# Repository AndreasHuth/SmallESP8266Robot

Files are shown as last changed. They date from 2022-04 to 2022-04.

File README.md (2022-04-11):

# Small ESP8266 Robot
## Short Description
This is a small 2-wheel robot project. Normally not very special. 😉

But there some special topics (at least for me 😊)
- My first project with a self developed PCB (made in China)
- Usage of standard components (easy to get and therefore cheap)
- Design with a standard 18650 Lipo (charging with a USB-C connector)
- 3d printed chassis with a nice design (made by me)
- Usage of an ESP8266 (Wemos D1 mini) with some special features:
        - programming via micro usb interface
        - Wifi access point to control the robot (very nice easy web-interface)
                Please have a look @ this repository 😊

## How to use
Please download the whole project and open it direktly in Visual Studio Code. 
PlatformIO Extension is necessary.

## further informations
Needed packages:
	links2004/WebSockets @ ^2.3.5
	bblanchon/ArduinoJson @ 5.13.3
	pololu/VL53L0X @ ^1.3.0

## Links

https://github.com/miharix/miharix-wifi-rc

## further informations / pictures

final robot :-) 

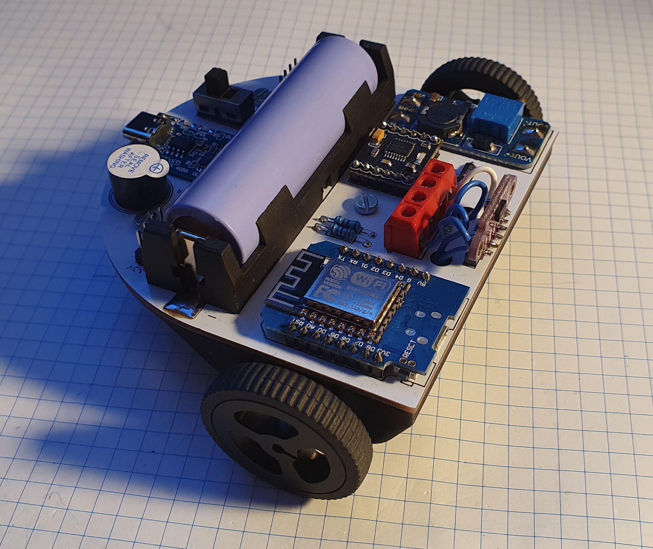
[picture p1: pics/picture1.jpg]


3D model: 

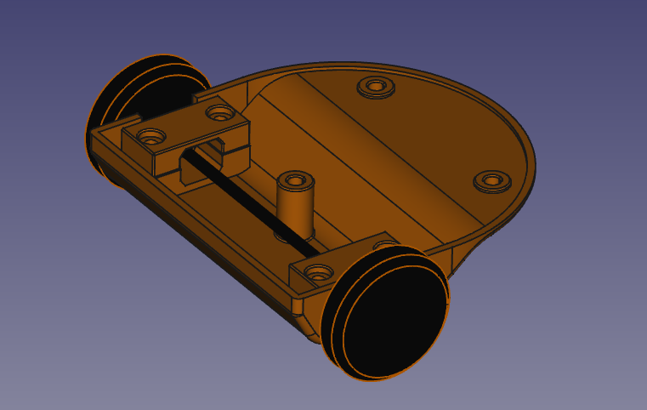
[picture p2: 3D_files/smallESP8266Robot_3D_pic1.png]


link to the schematic:

https://github.com/AndreasHuth/SmallESP8266Robot/blob/master/schematic/Schematic_SmallESP8266Robot.pdf

and partlist:

https://github.com/AndreasHuth/SmallESP8266Robot/blob/master/partlist/part_overview.txt

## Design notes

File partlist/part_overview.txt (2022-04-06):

partlist:
- WEMOS D1 MINI
- VL53LXX
- MOTOR DRIVER
- USB-C 18650 CHARGER
- MT3608 
- Buzzer
- Main switch 
- resistors

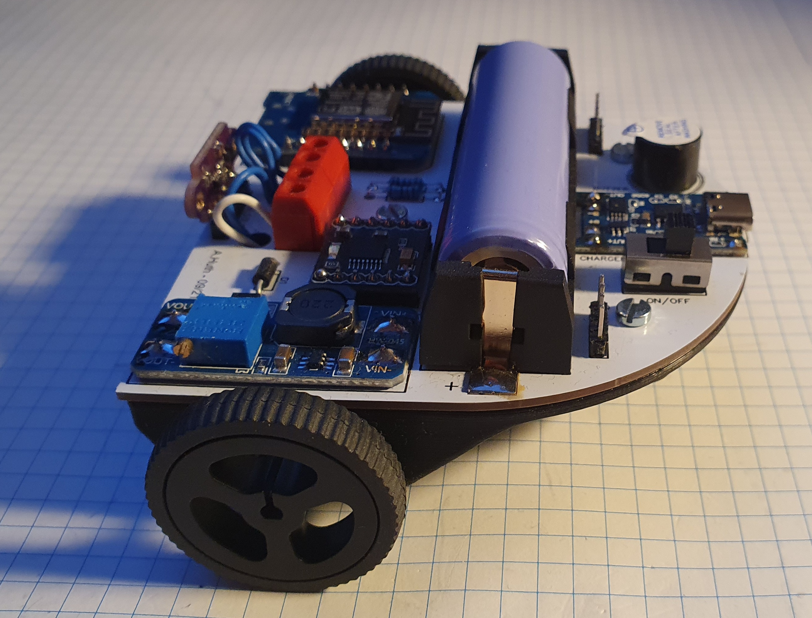
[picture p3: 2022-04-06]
pics/picture3.jpg

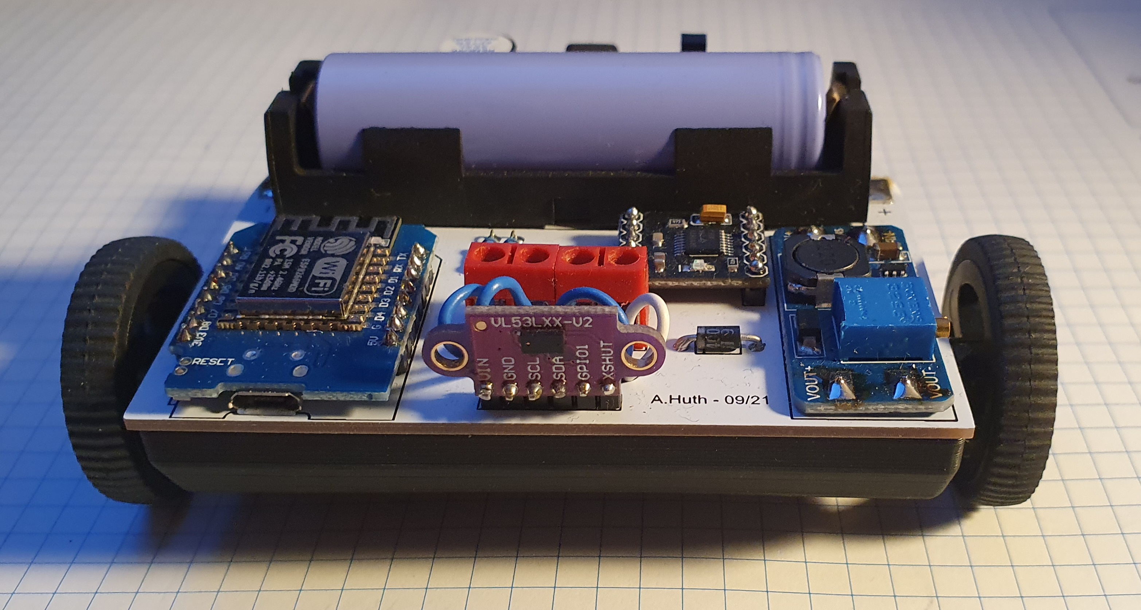
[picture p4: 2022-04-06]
pics/picture4.jpg

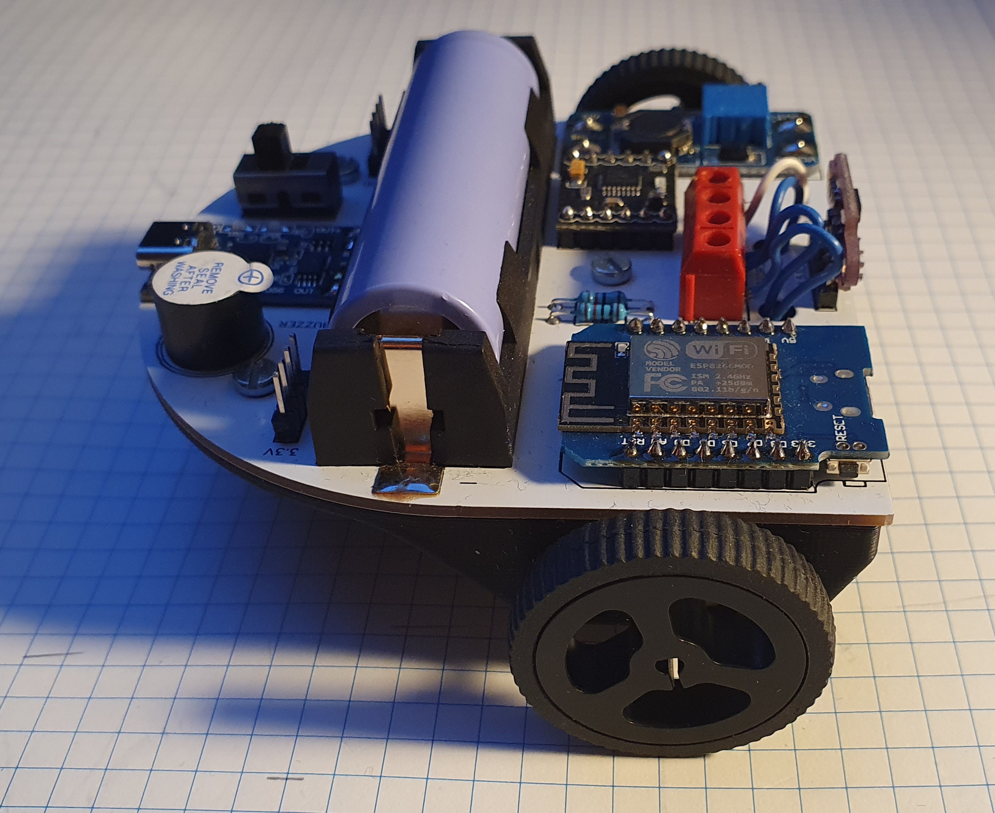
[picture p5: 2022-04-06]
pics/picture5.jpg

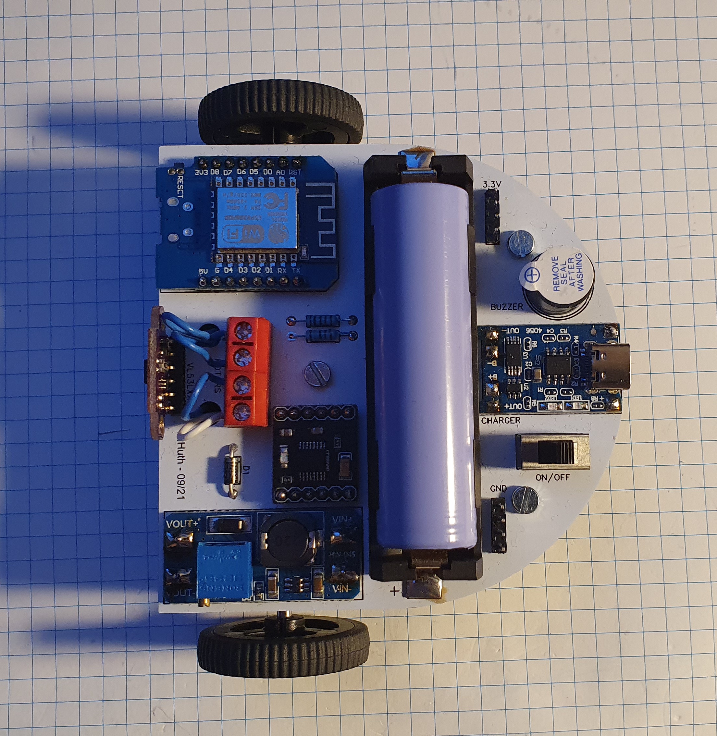
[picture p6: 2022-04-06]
pics/picture2.jpg

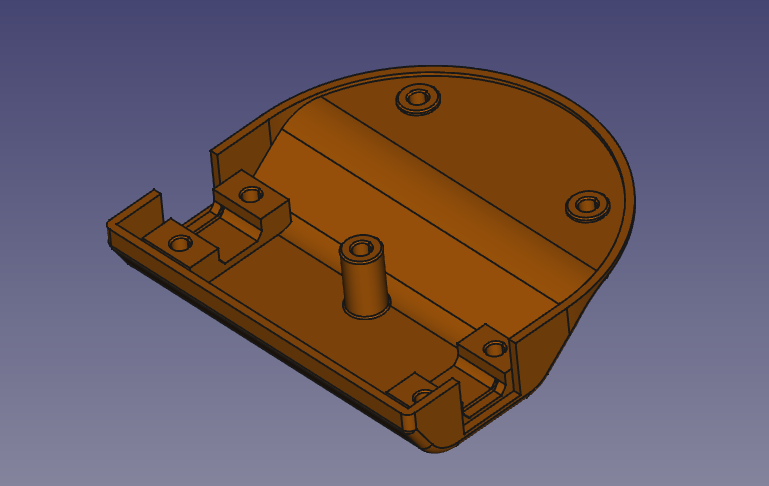
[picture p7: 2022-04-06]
3D_files/smallESP8266Robot_3D_pic2.png

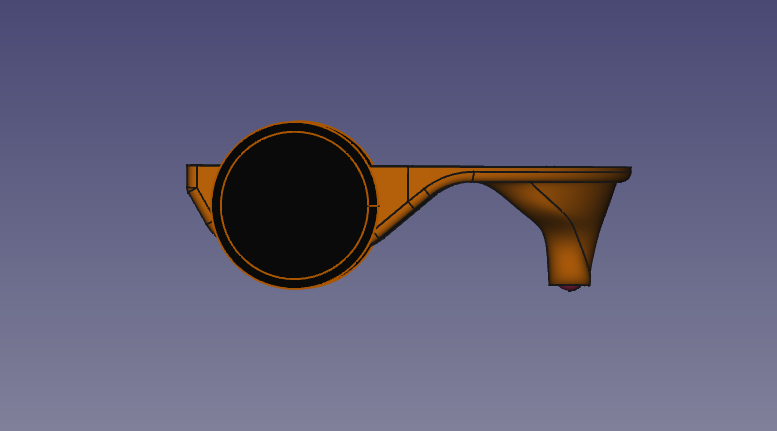
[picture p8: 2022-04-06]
3D_files/smallESP8266Robot_3D_pic3.png

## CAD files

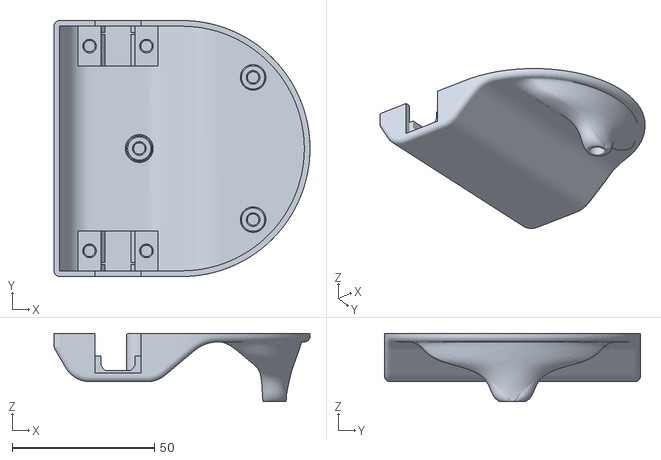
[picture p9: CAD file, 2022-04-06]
3D_files/chassiss_V1.stl
90.0 x 90.0 x 24.0

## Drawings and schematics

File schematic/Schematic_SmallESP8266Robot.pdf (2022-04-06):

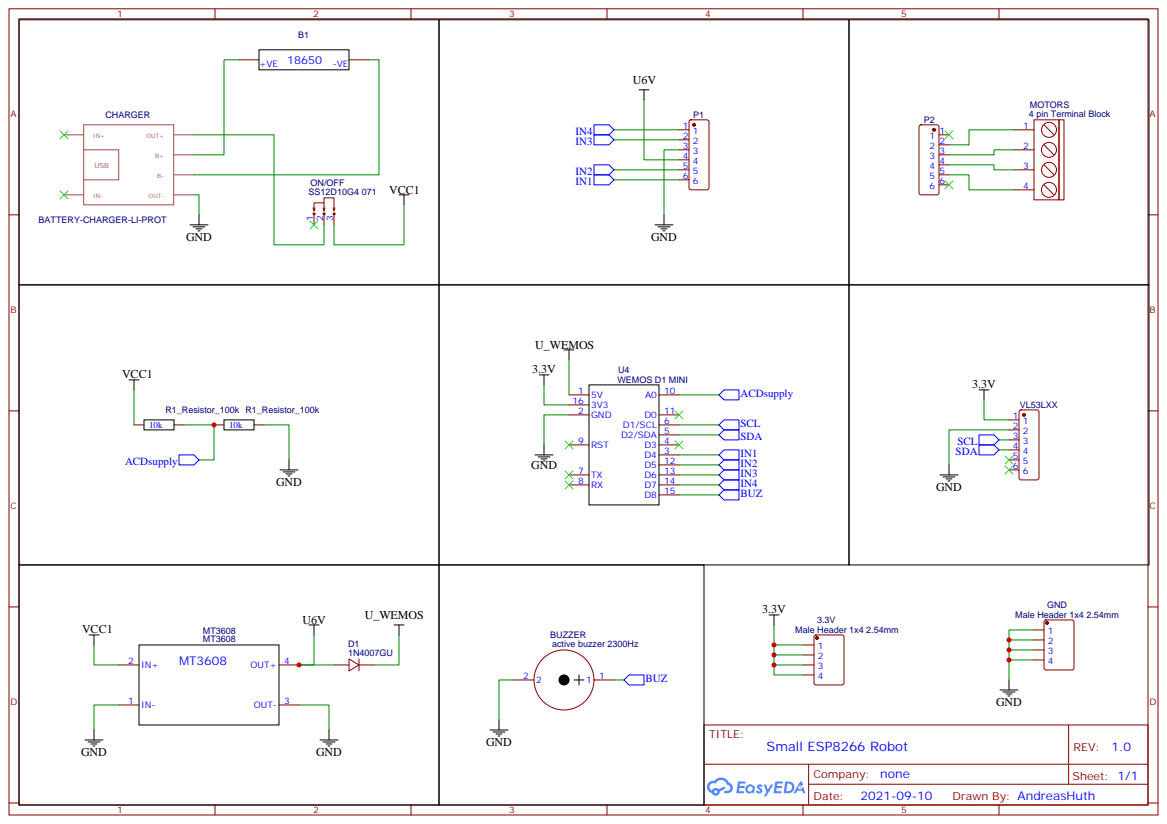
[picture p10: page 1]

BATTERY-CHARGER-LI-PROT

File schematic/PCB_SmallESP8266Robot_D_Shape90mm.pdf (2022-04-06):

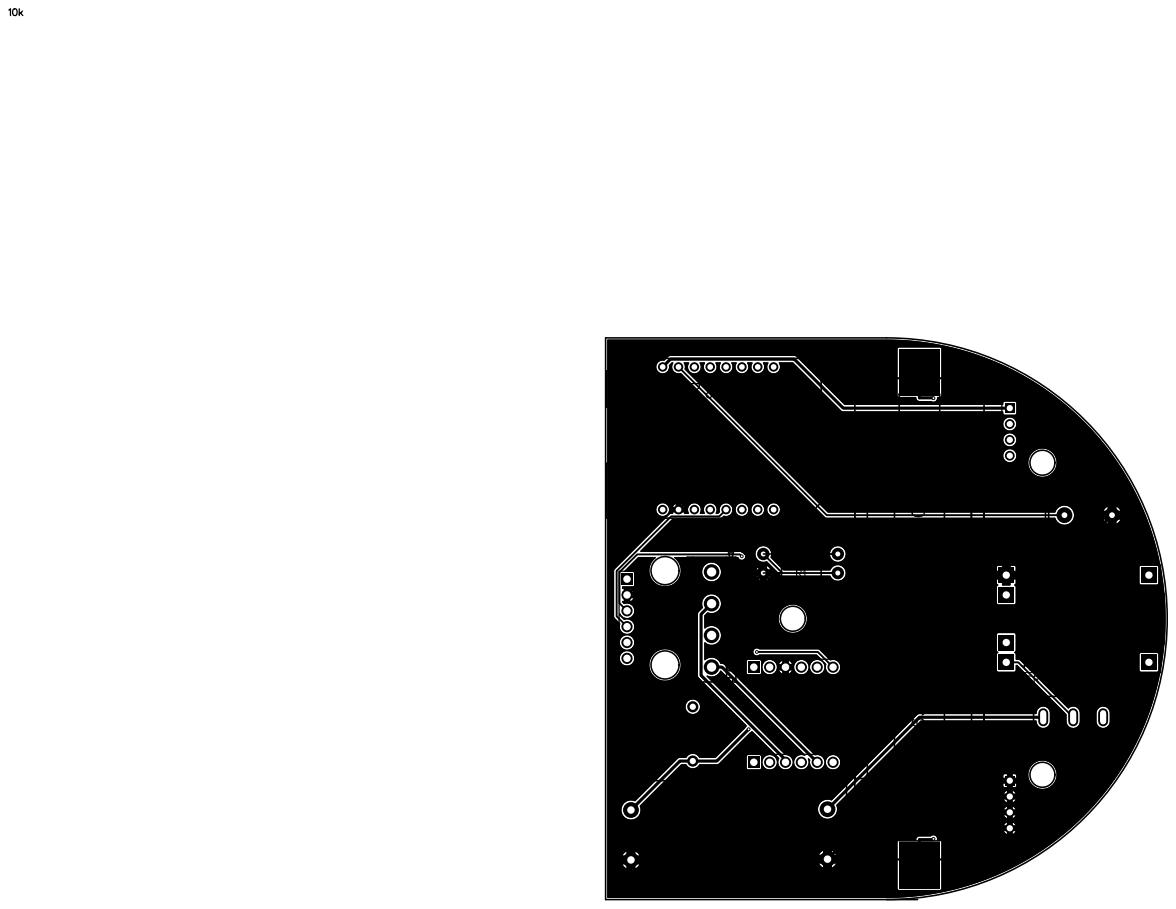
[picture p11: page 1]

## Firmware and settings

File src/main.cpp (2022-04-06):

#include "defines.h"
#include "lib.h"
#include "motors.h"
#include "globals.h"
#include "wifiRC.h"
#include "VL53lib.h"
unsigned long currentMillis = millis();
unsigned long previousMillis = 0;
unsigned long updateMillis = 0;

const long interval = 1000; //interval for checking failsave state

bool obstacle = false;


//#########################################################################################################

void setup() {
    initMotor();
    initBuzzer();
    VL53L0Xsetup();
    initRC ();
    delay (200);
    buzzerOn200ms();
}

//#########################################################################################################

void loop(void) {

  ResetToFactory();
  webSocket.loop();

  currentMillis = millis();
  if (currentMillis - previousMillis >= interval) {
#ifdef DEBUG
    Serial.printf("S1_6_flag=%d\n", S1_6_flag);
#endif
    previousMillis = currentMillis;
    if (S1_6_flag == false) {
      SameStateCount++;
      if (SameStateCount >= FailSaveTime) {
        stopMotor();
        }
    } else {
      SameStateCount = 0;
      S1_6_flag = false;
    }

    VL53L0Xloop();
    getLipoVoltage(); 
    
  }
  if (SameStateCount < FailSaveTime) {
    if (connected){
      if (currentMillis - updateMillis >= CONTROLINTERVAL) {
        updateMillis = currentMillis;
        if (VL53L0Xloop() < 150) {
          obstacle = true;
        } else {
          obstacle = false;
        }
          CalcSetMotorSpeed(obstacle);
      }
    }
    else{
      stopMotor();
    }
  }
  server.handleClient();
}

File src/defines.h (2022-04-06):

/*
 * defines.h
 *
 *  Created on: 25.09.2017
 *      Author: anonymous
 */

#ifndef DEFINES_H_
#define DEFINES_H_

#define PIN_MOTOR2_PWM 14        //D2
#define PIN_MOTOR2_DIR 2        

#define PIN_MOTOR1_PWM 13       
#define PIN_MOTOR1_DIR 12       

#define PIN_BUZZER 15       


#define HARD_RESET_PIN  0        // D3

#define CONTROLINTERVAL 120

#define MAX_ACCEL       40

#define MOTOROFFSET     200
#define MAXSPEED        1020

#define STOPDISTANCE    9

// Telemetry
#define TELEMETRY_BATTERY 1
#define TELEMETRY_ANGLE 1
//#define TELEMETRY_DEBUG 1  // Dont use TELEMETRY_ANGLE and TELEMETRY_DEBUG at the same time!

//#define DEBUG
#define DEBUG1
#define DEBUG2

#define PRINTLN(var) Serial.print(#var ": "); Serial.println(var)

#endif /* DEFINES_H_ */

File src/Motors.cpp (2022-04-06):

/*
 * Motors.cpp
 *
 *  Created on: 25.09.2017
 *      Author: anonymous
 */

#include "defines.h"
#include "globals.h"


// ########################################################################################

void stopMotor(void)
{
    analogWriteRange(1023); 
    digitalWrite(PIN_MOTOR1_DIR, LOW);
    digitalWrite(PIN_MOTOR1_PWM, LOW);
    digitalWrite(PIN_MOTOR2_DIR, LOW);
    digitalWrite(PIN_MOTOR2_PWM, LOW);
}

// ########################################################################################

void initMotor(void)
{
    
    pinMode(PIN_MOTOR1_DIR, OUTPUT);
    pinMode(PIN_MOTOR1_PWM, OUTPUT);
    pinMode(PIN_MOTOR2_DIR, OUTPUT);
    pinMode(PIN_MOTOR2_PWM, OUTPUT);

    stopMotor();
}

// ########################################################################################

const byte controllerFA = 10; //PWM FORWARD PIN for OSMC Controller A (left motor)
const byte controllerRA = 9;  //PWM REVERSE PIN for OSMC Controller A (left motor)

const byte controllerFB = 6;  //PWM FORWARD PIN for OSMC Controller B (right motor)
const byte controllerRB = 5;  //PWM REVERSE PIN for OSMC Controller B (right motor)

int throttle, direction = 0; //throttle (Y axis) and direction (X axis) 

int leftMotor,leftMotorScaled = 0; //left Motor helper variables
float leftMotorScale = 0;

int rightMotor,rightMotorScaled = 0; //right Motor helper variables
float rightMotorScale = 0;

float maxMotorScale = 0; //holds the mixed output scaling factor

int deadZone = 10; //jostick dead zone 

void CalcSetMotorSpeed (bool disappear)
{
    // Wertebereich 0...180
    direction = (int) strtol(S1_buff, NULL, 16);
    throttle = (int) strtol(S2_buff, NULL, 16);

    // Wertebereich -90...+90
    direction -= 90;
    throttle -= 90;

    // Wertebereich  auf -1000 ... +1000 erweitern 
    direction *= 100;    direction /=   9;
    throttle *= 100;    throttle /=   9;

    //mix throttle and direction
    leftMotor = throttle+direction;
    rightMotor = throttle-direction;

  #ifdef DEBUG
    //print the initial mix results
    Serial.print("LIN:"); Serial.print( leftMotor, DEC);
    Serial.print(", RIN:"); Serial.print( rightMotor, DEC);
  #endif
    //calculate the scale of the results in comparision base 8 bit PWM resolution
    leftMotorScale =  leftMotor/1000.0;
    leftMotorScale = abs(leftMotorScale);
    rightMotorScale =  rightMotor/1000.0;
    rightMotorScale = abs(rightMotorScale);

  #ifdef DEBUG
    Serial.print("| LSCALE:"); Serial.print( leftMotorScale,2);
    Serial.print(", RSCALE:"); Serial.print( rightMotorScale,2);
  #endif
    //choose the max scale value if it is above 1
    maxMotorScale = max(leftMotorScale,rightMotorScale);
    maxMotorScale = max((float)1.0,maxMotorScale);

    //and apply it to the mixed values
    leftMotorScaled = constrain(leftMotor/maxMotorScale,-1000,1000);
    rightMotorScaled = constrain(rightMotor/maxMotorScale,-1000,1000);

  #ifdef DEBUG
    Serial.print("| LOUT:"); Serial.print( leftMotorScaled);
    Serial.print(", ROUT:"); Serial.print( rightMotorScaled);

    Serial.print(" |");
  #endif

    //apply the results to appropriate uC PWM outputs for the LEFT motor:
    if(abs(leftMotorScaled)>deadZone)
    {
        if (leftMotorScaled > 0)
        {
          #ifdef DEBUG
            Serial.print("F");
            Serial.print(abs(leftMotorScaled),DEC);
          #endif
          
            if (!disappear){
                digitalWrite(PIN_MOTOR1_DIR, LOW);
                analogWrite(PIN_MOTOR1_PWM, abs(leftMotorScaled));       
            }
            else
            {
                digitalWrite(PIN_MOTOR1_DIR, LOW);
                digitalWrite(PIN_MOTOR1_PWM, LOW);
            }

        }
        else 
        {          
      #ifdef DEBUG
        Serial.print("R");
        Serial.print(abs(leftMotorScaled),DEC);
      #endif

        digitalWrite(PIN_MOTOR1_DIR, HIGH);
        analogWrite(PIN_MOTOR1_PWM, 1000-abs(leftMotorScaled));
        }
    }  
    else 
    {
  #ifdef DEBUG       
    Serial.print("IDLE");   
  #endif
    digitalWrite(PIN_MOTOR1_DIR, LOW);
    digitalWrite(PIN_MOTOR1_PWM, LOW);
    } 

    //apply the results to appropriate uC PWM outputs for the RIGHT motor:  
    if(abs(rightMotorScaled)>deadZone)
    {

        if (rightMotorScaled > 0)
        {  
          #ifdef DEBUG  
            Serial.print("F");
            Serial.print(abs(rightMotorScaled),DEC);
          #endif
          
            if (!disappear){
                digitalWrite(PIN_MOTOR2_DIR, LOW);
                analogWrite(PIN_MOTOR2_PWM, abs(rightMotorScaled));
            }
            else
            {
                digitalWrite(PIN_MOTOR2_DIR, LOW);
                digitalWrite(PIN_MOTOR2_PWM, LOW);    
            }
        }
        else 
        {   
          #ifdef DEBUG  
            Serial.print("R");
            Serial.print(abs(rightMotorScaled),DEC);
          #endif

            digitalWrite(PIN_MOTOR2_DIR, HIGH);
            analogWrite(PIN_MOTOR2_PWM, 1024-abs(rightMotorScaled));
        }
    }  
    else 
    {
  #ifdef DEBUG          
    Serial.print("IDLE");
  #endif
    
    digitalWrite(PIN_MOTOR2_DIR, LOW);
    digitalWrite(PIN_MOTOR2_PWM, LOW);
    } 

  #ifdef DEBUG  
    Serial.println("");
  #endif

  //To do: throttle change limiting, to avoid radical changes of direction for large DC motors
}

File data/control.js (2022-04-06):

   var Servo1=0;
    var Servo2=0;
    var Servo3=0;
    var Servo4=0;
    var Servo5=0;
    var Servo6=0;
    
    var connection = new WebSocket('ws://'+location.hostname+':81/', ['arduino']);
    connection.onopen = function () {
   //   connection.send('Connect ' + new Date()); 
    };
    connection.onerror = function (error) {
      console.log('WebSocket Error ', error);
    };
    connection.onmessage = function (e) {
      console.log('Server: ', e.data);
    };

    function sendServo2(){
	var S3 = "0";
	var S4 = "0";    
	var S5 = "0";
	var S6 = "0";

	Servo1=Servo1/90-1
	Servo2=Servo2/90-1
//https://electronics.stackexchange.com/questions/19669/algorithm-for-mixing-2-axis-analog-input-to-control-a-differential-motor-drive
	//convert to polar   
    	r = Math.hypot(Servo2, Servo1)
	t = Math.atan2(Servo1, Servo2)
	
	//rotate by 45 degrees
	t += Math.PI / 4
	//back to cartesian
	Servo1 = r * Math.cos(t)
	Servo2 = r * Math.sin(t)
	//rescale the new coords
	Servo1 = Servo1 * Math.sqrt(2)
	Servo2 = Servo2 * Math.sqrt(2)
	//clamp to -1/+1
	Servo1 = Math.max(-1, Math.min(Servo1, 1))
	Servo2 = Math.max(-1, Math.min(Servo2, 1))

	Servo1=(Servo1+1)*90
	Servo2=(Servo2+1)*90
  //Servo1=(Servo1)*90
	//Servo2=(Servo2)*90
  

	S2 =parseInt(Servo1).toString(16);
      	S1 =parseInt(Servo2).toString(16);

	if(S1.length < 2) { S1 = '0' + S1; }
        if(S2.length < 2) { S2 = '0' + S2; }
	if(S3.length < 2) { S3 = '0' + S3; }
	if(S4.length < 2) { S4 = '0' + S4; }
	if(S5.length < 2) { S5 = '0' + S5; }
	if(S6.length < 2) { S6 = '0' + S6; }
	//console.clear();
	//console.log('S1: ' + S1+' S2: ' + S2);
	//console.log('Servo1: ' + Servo1+' Servo2: ' + Servo2);
        
	var S1_6 = S1+S2+S3+S4+S5+S6;
        //console.log('S1_6: ' + S1_6);
        connection.send('S'+S1_6+'\n');

    }

    function sendServo(){
      S1 =parseInt(Servo1).toString(16);
      S2 =parseInt(Servo2).toString(16);
      var S3 = "0";
      var S4 = "0";    
      var S5 = "0";
      var S6 = "0";
      
      if(S1.length < 2) { S1 = '0' + S1; }
      if(S2.length < 2) { S2 = '0' + S2; }
      if(S3.length < 2) { S3 = '0' + S3; }
      if(S4.length < 2) { S4 = '0' + S4; }
      if(S5.length < 2) { S5 = '0' + S5; }
      if(S6.length < 2) { S6 = '0' + S6; }
	//console.clear();
	//console.log('O1: ' + O1+' O2: ' + O2);
      //console.log('Servo1: ' + Servo1+' Servo2: ' + Servo2);
      var S1_6 = S1+S2+S3+S4+S5+S6;

     // console.log('S1_6: ' + S1_6);
      connection.send('S'+S1_6+'\n');
     }
